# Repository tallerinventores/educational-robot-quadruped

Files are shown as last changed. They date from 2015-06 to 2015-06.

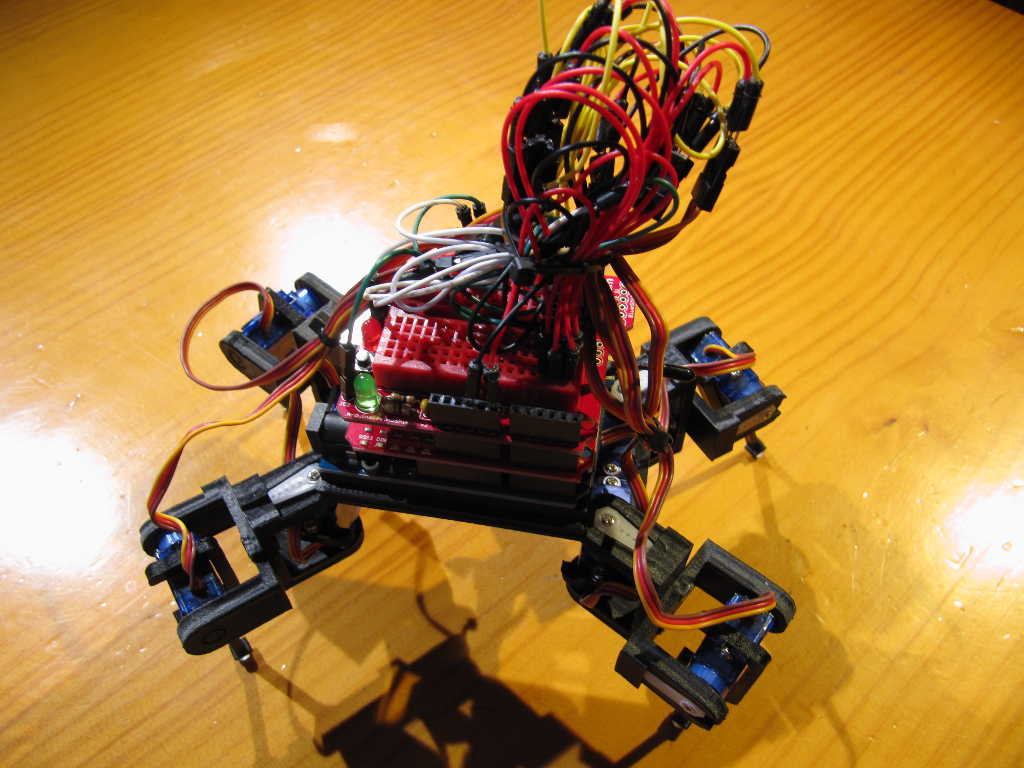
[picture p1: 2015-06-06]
img/photo-erq-2.png

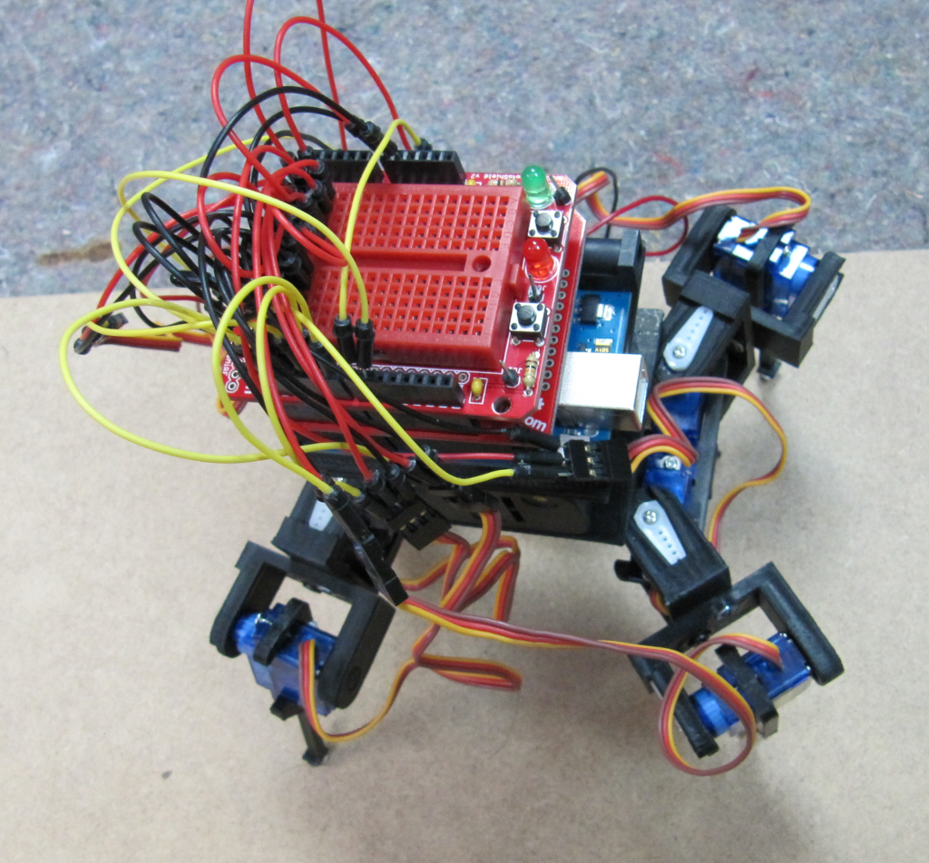
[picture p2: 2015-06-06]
img/photo-erq-1.png

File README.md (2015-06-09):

# Educational Robot Quadruped #

> Quadruped robot for educational use

* * *

## Resumen ##

Cuadrúpedo robótico para uso en entornos educativos. El cuadrúpedo ha sido
desarrollado y optimizado para impresión 3D y pensando en su bajo coste y
facilidad de montaje y uso. Permite ser controlado desde diferentes plataformas.

## Instalación ##

En esta sección se cubre la instalación de software y hardware para el montaje
recomendado, mediante [Scratch](https://scratch.mit.edu/) y
[Arduino](http://www.arduino.cc/).

### Requerimientos de software ###

Para poder usar Scratch (v2.0 online) con Arduino, es necesario
[s2a_fm](https://github.com/MrYsLab/s2a_fm) una extensión de Scratch para
comunicarse con Arduino. Para generar los archivos aptos para la impresora 3D
desde los archivos `.stl` será necesario adicionalmente un software para esta
función, como puede ser [Slic3r](http://slic3r.org/).

Ver los requerimientos de mencionados programas previamente.

### Requerimientos de hardware ###

Será necesario para su montaje y uso una fuente de alimentación que proporcione
10W a 5V, un Arduino Uno o equivalente, una pareja de XBEE previamente
asociados, un explorer de XBEE, un shield de XBEE, ocho servomotores tipo 9g con
sus correspondientes accesorios (tornillos y cuernos). El cuadrúpedo está
optimizado para usar los servos **TowerPro SG90**. Adicionalmente harán falta
tornillos de métrica tres de diferentes largos.

## Uso ##

Instrucciones de montaje y puesta en marcha.

### Montaje del cuadrúpedo robótico ###

1.  Imprimir una unidad de los archivos `chassis.stl`, `arduino_base.stl`,
    `tray.stl`. Imprimir cuatro unidades de `leg.stl`. Imprimir ocho unidades de
    `servo_button.stl`, `shoulder.stl`. Puede ser necesario repasar las piezas
    impresas con el fin de eliminar rebabas.  
2.  Atornillar cuatro servos sobre el chasis (_chassis_) usando los tornillos de
    montaje proporcionados por los servos. Los ejes de los servos han de quedar
    hacia el exterior.  
3.  Montar un servo en cada pata (_leg_) con el eje en el extremo contrario a la
    base de la pata. Atornillarlos con los tornillos correspondientes.  
4.  Unir parejar de soportes (_shoulder_) usando dos tornillos M3x6 con tuerca.  
5.  Para cada soporte: Colocar un cuerno del servo y un rodamiento
    (_servo\_button_) dentro del soporte. Encajar un servo dentro del soporte y
    atornillarlo, asegurando que puede hacer la rotación completa.  
6.  Encajar dos tuercas en la bandeja (_tray_). Presionar contra el chasis hasta
    que encaje.  
7.  Si se va a usar portapilas, éste irá entre la bandeja y la base del Arduino.
    Ambas piezas se unen con tornillos de M3x35 en caso de usarse portapilas o
    de M3x10 en caso contrario.  
8.  Encastrar cuatro tuercas en la base del Arduino (_arduino\_base_), fijar el
    Arduino a su base mediante tornillos M3x10.

### Conexión eléctrica ###

Todas las alimentaciones de los servomotores van en paralelo y a la fuente de
alimentación. Las señales de control de los servos van a Arduino, usando las
conexiones del dos al cinco para los servos más cercanos al cuerpo, en sentido
contrario a las agujas del reloj empezando por la esquina superior izquieda
(extremo contrario a la conexión USB de Arduino). Los servos de las patas usan
las conexiones del seis a la nueve, numerados de la misma manera. La masa del
Arduino y de la fuente de alimentación ha de ser compartida. Conectar el shield
de XBEE sobre el Arduino. Conectar el explorer de XBEE a un puerto USB libre del
ordenador a usar.

### Firmware ###

El Arduino deberá tener cargado el firmware Firmata (incluido con Arduino IDE
bajo en nombre de `StandardFirmata`).

### Software ###

Con el explorer de XBEE conectado al ordenador, lanzar s2a_fm con el nombre del
puerto donde realizar la comunicación con XBEE. Por ejemplo:

        python s2a_fm.py /dev/ttyUSB0

Abrir Scratch y cargar el proyecto `educational-robot-quadruped.sb2`, una vez
hecho, se podrá ver en la interfaz gráfica los posibles movimientos del
cuadrúpedo en forma de flechas para dichas órdenes.

El cuadrúpedo sólo avanzará un paso en la dirección elegida, y sólo si
previamente se ha levantado. El botón de stop permite cancelar cualquier orden,
deshabilitar el robot y parar el programa. Después de pulsarlo será necesario
volver a iniciar el proyecto de Scratch.

### Bugs ###

Se han observado los siguientes problemas:

-   Desde la posición de reposo, el cuadrúpedo presenta demasiada carga para
    los servos puede levantarse.  
-   El software de control provoca al inicio movimientos extraños.  
-   En determinados momentos hay servos que se deshabilitan sin razón aparente.
    (Problema de PyMata?).  
-   Por protocolo de Firmata, es necesario un pequeño tiempo entre órdenes para
    asegurar que son recibidas y procesadas. (Implementado).

## Enlaces externos ##

Este proyecto también está presente en:

-   [Scratch](https://scratch.mit.edu/projects/65799474/).  
-   [Thingiverse](http://www.thingiverse.com/thing:756995).

## Créditos ##

Proyecto realizado por Taller de Inventores 2015, representado por:

-   kwendenarmo <kwendenarmo@akornsys-rdi.net>

Alumnos de Centro de Formación Padre Piquer:

-   C, Duanju  
-   D, Diego

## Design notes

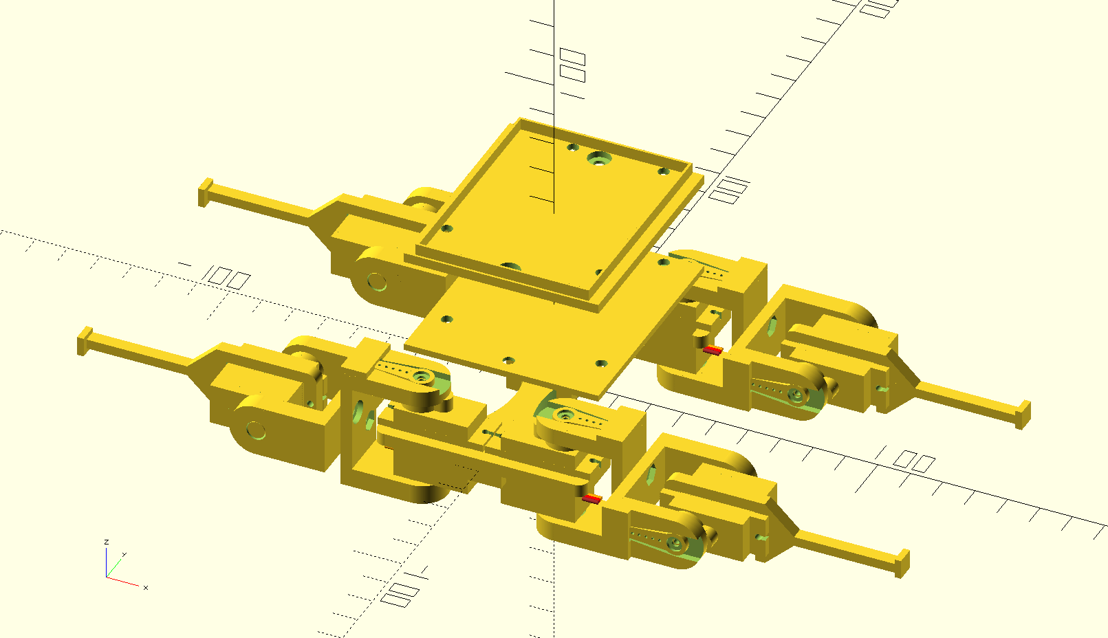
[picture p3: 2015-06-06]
img/render.png

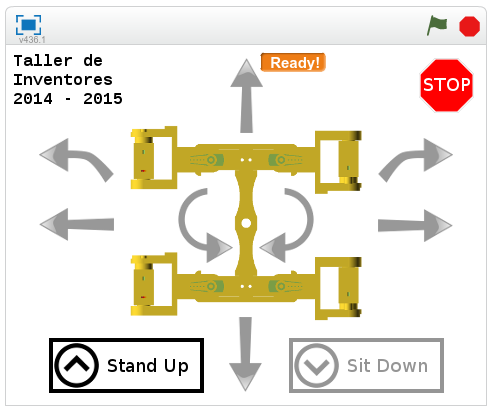
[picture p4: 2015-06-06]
img/scratch-snapshop.png

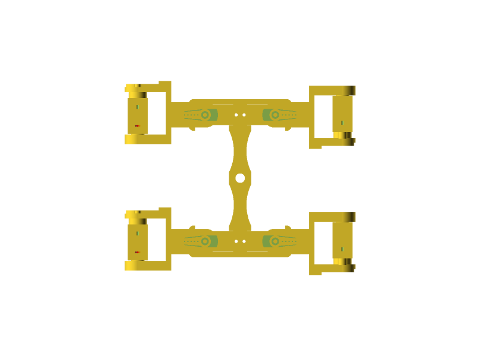
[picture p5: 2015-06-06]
scratch/res/robot_scaled.png

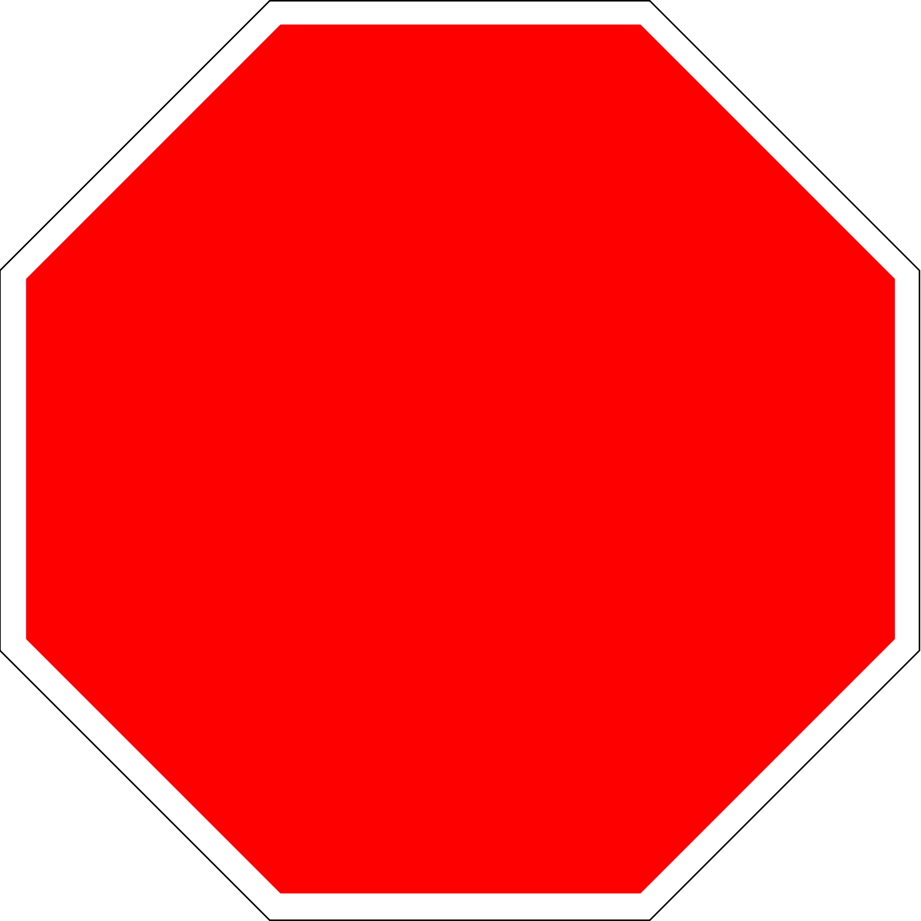
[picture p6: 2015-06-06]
scratch/res/2000px-Blank_stop_sign_octagon.svg.png

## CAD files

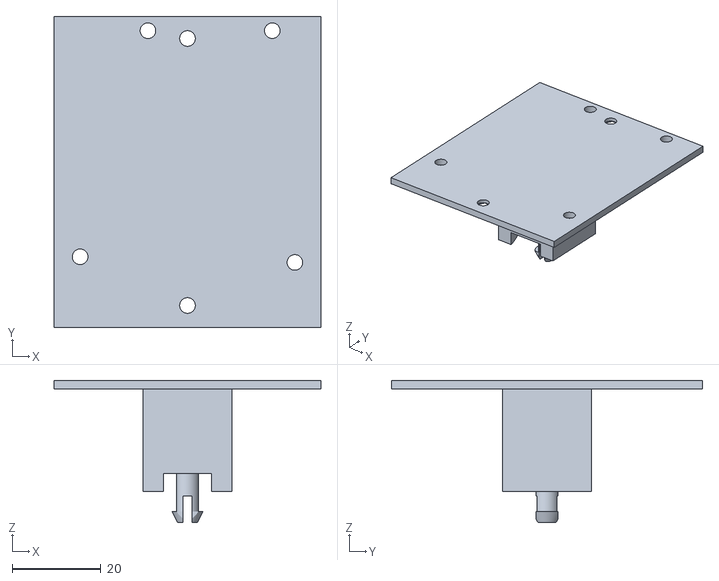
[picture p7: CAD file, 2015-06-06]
3d/tray.stl
60.0 x 70.0 x 32.0

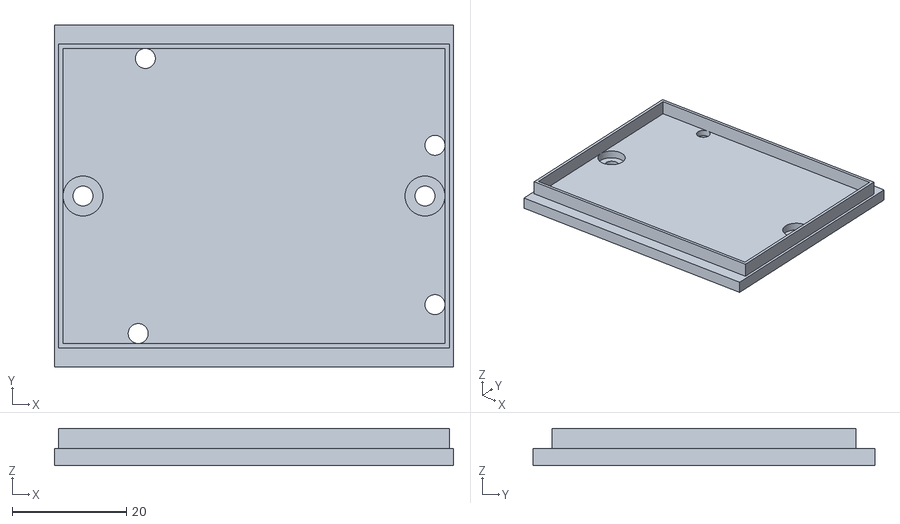
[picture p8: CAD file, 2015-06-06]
3d/arduino_base.stl
70.0 x 60.0 x 6.56

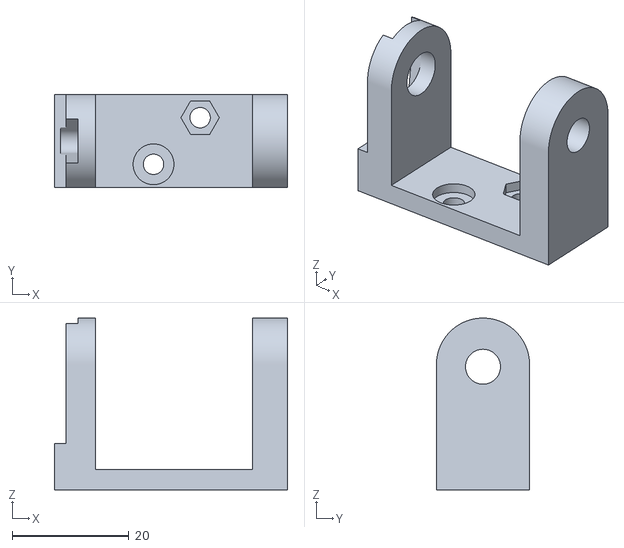
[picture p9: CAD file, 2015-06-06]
3d/shoulder.stl
40.0 x 16.0 x 29.5

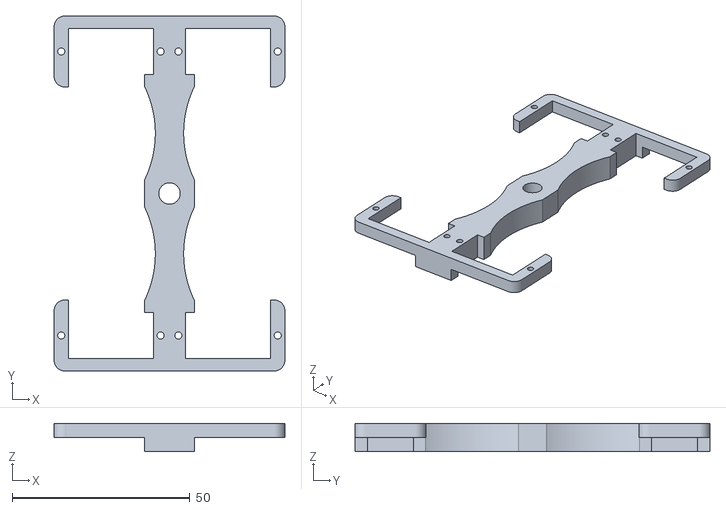
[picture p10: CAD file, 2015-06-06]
3d/chassis.stl
65.0 x 100.0 x 8.00

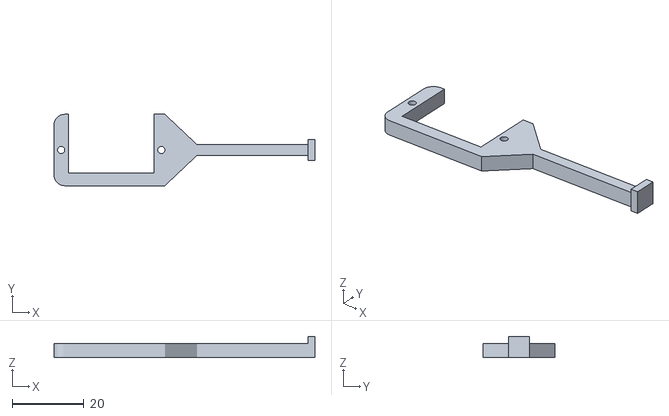
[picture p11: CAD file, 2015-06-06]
3d/leg.stl
73.0 x 20.0 x 6.00

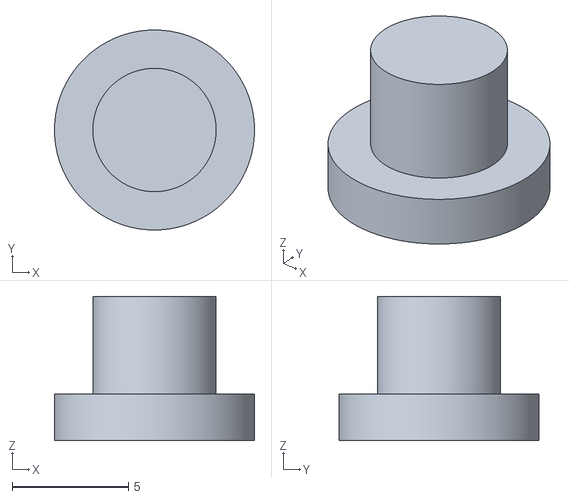
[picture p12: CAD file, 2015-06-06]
3d/servo_button.stl
8.60 x 8.60 x 6.19

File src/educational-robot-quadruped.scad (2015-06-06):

/* {{{ %%SECTION_HEADER%%
 * * * *
 * This header information is automatically generated by KodeUtils.
 *
 * File 'educational-robot-quadruped.scad' edited by kwendenarmo,
 * last modified: 2015-06-06.
 * This file is part of 'Educational robot quadruped' package, please see the
 * readme files for more information about this file and this package.
 *
 * Copyright (C) 2015 by kwendenarmo <kwendenarmo@akornsys-rdi.net>
 * Released under the GNU GPLv3
 * Original design 'Mini Quadruped - optimized for 9G servos' by TheCase
 * is licensed under the Creative Commons - Attribution license.
 * <http://www.thingiverse.com/thing:38159>
 *
 *    This program is free software: you can redistribute it and/or modify
 *    it under the terms of the GNU General Public License as published by
 *    the Free Software Foundation, either version 3 of the License, or
 *    (at your option) any later version.
 *
 *    This program is distributed in the hope that it will be useful,
 *    but WITHOUT ANY WARRANTY; without even the implied warranty of
 *    MERCHANTABILITY or FITNESS FOR A PARTICULAR PURPOSE.  See the
 *    GNU General Public License for more details.
 *
 *    You should have received a copy of the GNU General Public License
 *    along with this program.  If not, see <http://www.gnu.org/licenses/>.
 *
 * * * *
 * %%EOS_HEADER%% }}}
 */

$fn=360;

bb_length=100;
bb_width=14;
bb_height=8;

/* uncomment for generic 9g
servo_length = 23;
servo_width = 12.5;
servo_tall = 26;        //top to bottom of servo casing (w/o drive gear)
servo_clear = 5.5;      //servo clearance from inside shoulder wall
horn_radius1 = 3.5;
horn_radius2 = 2;
horn_rdist = 13;
*/

// tower pro 9g
servo_length = 24;
servo_width = 13;
servo_tall = 27;
servo_clear = 7;
horn_radius1 = 3.8;
horn_radius2 = 2.1;
horn_rdist = 14.6;
servo_hole_r = 1;

show_full_assembly = 1;
showservos = 1;
h_pos = (bb_length-20)/2;

/* individual parts (for export) - uncomment one line at a time */
if (show_full_assembly == 0) {
    //porta_arduino();
    //tray();
    //chassis();
    //backbone(bb_length,bb_width,bb_height,servo_length,servo_width);  //use chassis instead!
    //hip(servo_length,servo_width);  //use chassis instead!
    //leg(servo_length,servo_width);
    //servo_button();
    //shoulder(servo_tall,servo_clear,horn_radius1,horn_radius2,horn_rdist);
}

if (show_full_assembly == 1) {
    //full assembly example

    /*
    distribution
    3   4
    2   1
    */

    translate([0,0,-7]) tray();
    translate([0,0,53]) rotate([0,0,90]) porta_arduino();
    chassis();

    translate([22.25,-40,15.15]) rotate([0,0,0]) servo9g(0);
    translate([-22.25,-40,15.15]) rotate([0,0,180]) servo9g(0);
    translate([-22.25,40,15.15]) rotate([0,0,180]) servo9g(0);
    translate([22.25,40,15.15]) rotate([0,0,0]) servo9g(0);

    translate([h_pos+3.5,-h_pos,0]) rotate([0,-270,180]) shoulder(servo_tall,servo_clear,horn_radius1,horn_radius2,horn_rdist);
    translate([-h_pos-3.5,-h_pos,0]) rotate([0,90,0]) shoulder(servo_tall,servo_clear,horn_radius1,horn_radius2,horn_rdist);
    translate([-h_pos-3.5,h_pos,0]) rotate([0,90,0]) shoulder(servo_tall,servo_clear,horn_radius1,horn_radius2,horn_rdist);
    translate([h_pos+3.5,h_pos,0]) rotate([0,-270,180]) shoulder(servo_tall,servo_clear,horn_radius1,horn_radius2,horn_rdist);

    translate([22.25,-40,-11.75]) rotate([180,0,0]) servo_button();
    translate([-22.25,-40,-11.75]) rotate([180,0,0]) servo_button();
    translate([-22.25,40,-11.75]) rotate([180,0,0]) servo_button();
    translate([22.25,40,-11.75]) rotate([180,0,0]) servo_button();

    translate([h_pos+3.5,-h_pos,0]) rotate([90,0,90]) shoulder(servo_tall,servo_clear,horn_radius1,horn_radius2,horn_rdist);
    translate([-h_pos-3.5,-h_pos,0]) rotate([90,0,-90]) shoulder(servo_tall,servo_clear,horn_radius1,horn_radius2,horn_rdist);
    translate([-h_pos-3.5,h_pos,0]) rotate([90,0,-90]) shoulder(servo_tall,servo_clear,horn_radius1,horn_radius2,horn_rdist);
    translate([h_pos+3.5,h_pos,0]) rotate([90,0,90]) shoulder(servo_tall,servo_clear,horn_radius1,horn_radius2,horn_rdist);

    translate([64.75,-55,0]) rotate([-90,0,180]) servo9g(0);
    translate([-64.75,-25,0]) rotate([90,180,180]) servo9g(0);
    translate([-64.75,55,0]) rotate([90,180,180]) servo9g(0);
    translate([64.75,25,0]) rotate([-90,0,180]) servo9g(0);

    translate([64.75,-28,0]) rotate([270,0,0]) servo_button();
    translate([-64.75,-52,0]) rotate([90,0,0]) servo_button();
    translate([-64.75,28,0]) rotate([90,0,0]) servo_button();
    translate([64.75,52,0]) rotate([270,0,0]) servo_button();

    translate([h_pos*2+7.5,-h_pos-3.85,0]) rotate([270,0,0]) leg(servo_length,servo_width);
    translate([-h_pos*2-7.5,-h_pos+3.85,0]) rotate([90,180,0]) leg(servo_length,servo_width);
    translate([-h_pos*2-7.5,h_pos+3.85,0]) rotate([90,180,0]) leg(servo_length,servo_width);
    translate([h_pos*2+7.5,h_pos-3.85,0]) rotate([270,0,0]) leg(servo_length,servo_width);

}

module tray() {
    difference() {
        union() {
            translate([-30,-35,30]) cube([60,70,2]);
            cylinder(r=4, h=30);
            intersection() {
                union() {
                    for (i = [[34,17,6],[34,-17,6],[-34,17,6],[-34,-17,6]]) {
                        translate(i) cylinder(r=29.5,h=24);
                    }
                    translate([7.5,-4.5,6]) cube([3,9,24]);
                    translate([-10.5,-4.5,6]) cube([3,9,24]);
                    translate([-10,8,11]) cube([20,2,19]);
                    translate([-10,-10,11]) cube([20,2,19]);
                }
                translate([-10,-10,7]) cube([20,20,24]);
            }
        }
        union() {
            translate([0,0,-1]) difference() {
                union() {
                    cylinder(r=5, h=12);
                }
                union() {
                    translate([0,0,3]) cylinder(r=2.5, h=10);
                    translate([0,0,0.5]) cylinder(r1=2, r2=3.5, h=3);
                }
            }
            translate([-5,2.5,-1]) cube([10,4,4]);
            translate([-5,-6.5,-1]) cube([10,4,4]);
            translate([-1,-5,-1]) cube([2,10,7]);
            translate([0,-30,29]) cylinder(r=1.75, h=4);
            translate([0,-30,29.25]) cylinder(r=3.33, h=1.75, $fn=6);
            translate([0,30,29]) cylinder(r=1.75, h=4);
            translate([0,30,29.25]) cylinder(r=3.33, h=1.75, $fn=6);
            translate([24.13,-20.32,29]) cylinder(r=1.75, h=4);
            translate([-24.13,-19.05,29]) cylinder(r=1.75, h=4);
            translate([19.05,31.75,29]) cylinder(r=1.75, h=4);
            translate([-8.89,31.75,29]) cylinder(r=1.75, h=4);
        }
    }
}

module porta_arduino() {
    base_lenght = 70;
    base_width = 60;
    base_height = 3;
    ardu_lenght_mil = 2700;
    ardu_width_mil = 2100;
    ardu_height_mil = 40;
    ardu_hole1_x_mil = 550;
    ardu_hole1_y_mil = 100;
    ardu_hole2_x_mil = 600;
    ardu_hole2_y_mil = 2000;
    ardu_hole3_x_mil = 2600;
    ardu_hole3_y_mil = 300;
    ardu_hole4_x_mil = 2600;
    ardu_hole4_y_mil = 1400;
    outline = true;
    outline_width_mil = 30;
    outline_height_mil = 140;
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
